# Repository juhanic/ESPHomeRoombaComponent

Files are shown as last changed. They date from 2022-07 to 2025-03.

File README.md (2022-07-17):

# Roomba Component for ESPHome

  This is a quick and dirty update of [davidecavestro's work](https://github.com/davidecavestro/ESPHomeRoombaComponent) with a focus on giving a new user a reasonable chance of getting it working without digging through 100 forum threads. [This thread](https://community.home-assistant.io/t/add-wifi-to-an-older-roomba/23282/158) should be useful should there be any issues. I'll also be including my circuit board design for a small sandwich of boards that fit nicely on top of the roomba.
  
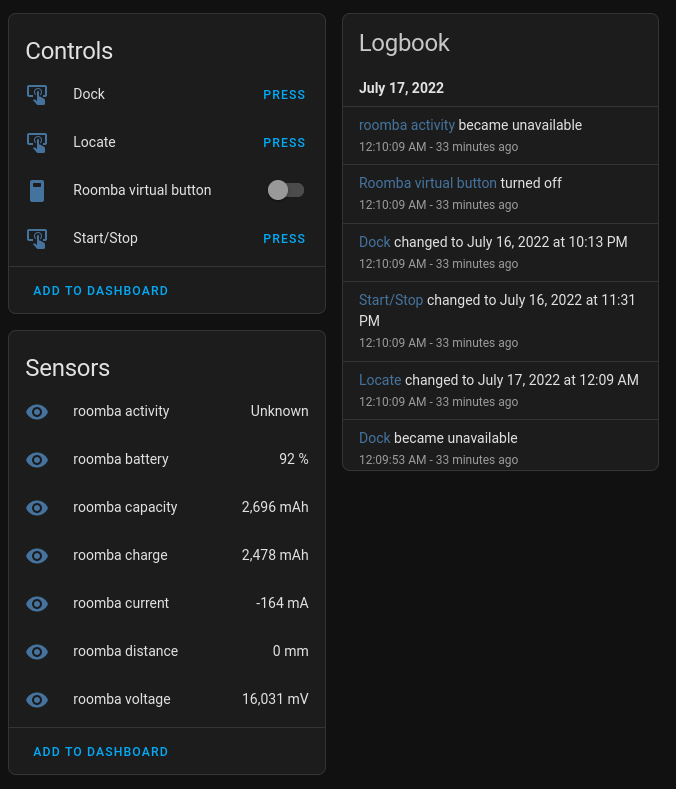
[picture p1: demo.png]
dashboard example
  I've added some notes and updates to the example in the example folder. My example config should get you up and running though there are a few bugs that still need to be worked out. 

  The inspiration is [Mannkind ESPHomeRoombaComponent](https://github.com/mannkind/ESPHomeRoombaComponent), that became deprecated due to dependency updates.
In addition I did not want the Roomba device to communicate over MQTT, it instead registers a service call for commands, and expose sensors through `roomba.yaml`.

## Hardware

## Wiring Guide
Using the brc pin we get the following:
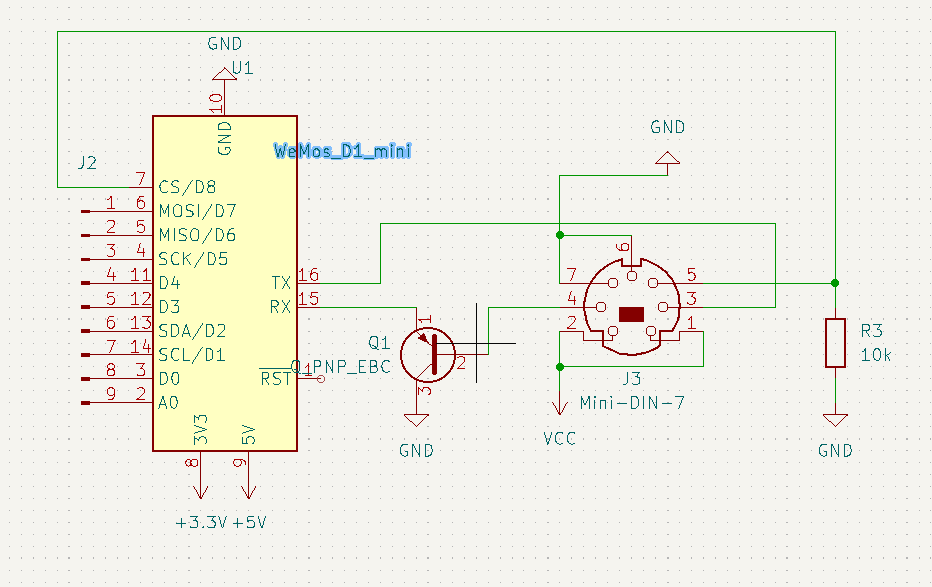
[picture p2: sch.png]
brc wiring

The PNP transistor is necessesary. Resistive dividers are hit or miss and a 2n4403 or a 2n3906 is cheap.

Alternatively using the IR led:
IR wiring

## Special Notes

*Depending on your Roomba model, you might be unlucky as me and have a bug that does not allow the device to wake from brc pin when it goes into passive mode during trickle charging. To circumvent this I copied my code from a previous general controller I had stationed in the kitchen for 433mhz and IR controlling that sends the start code with and IR led to the roomba, it need a clear sight of the roomba IR sensor over a short distance.

If you need this, uncomment the remote transmitter switch section in the `roomba.yaml` and use the switch to wake and clean. 

## Placement

The Wemos D1 mini is small enough to [fit into the compartment by one of the wheels](https://community-home-assistant-assets.s3.dualstack.us-west-2.amazonaws.com/optimized/2X/a/a258c7253f8bd3fe76ad9e7aa1202b60bd113d74_2_496x600.jpg). 
But using a esp-01 or esp-12 series and some single braid wire I have managed to fit it all under the top lid without bulging or deformeties, the only visual defect is my led that is pointing at the IR reciever.

## Custom Circuit Board

This board was designed to be etched at home but could also be ordered from the likes of dirtypcbs.com/ oshpark/ etc.  

If you want to recreate my circuit board exactly, you'll need:  
 - Wemos D1 Mini
 - USB Buck converter
 - 10K Resistor

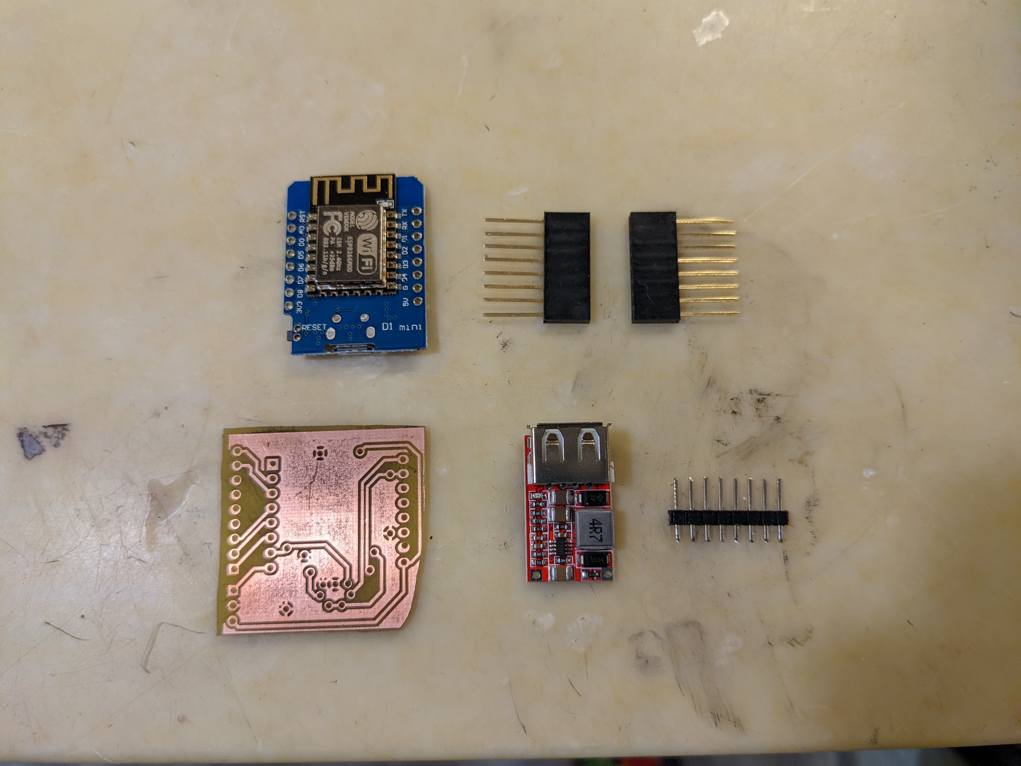
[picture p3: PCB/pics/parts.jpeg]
Parts


Pull 7 Header pins out of the pin headers that came with the Wemos D1 and stick them into the roomba's serial port, then place the board on top and solder the pins in place to get the alignment correct.  

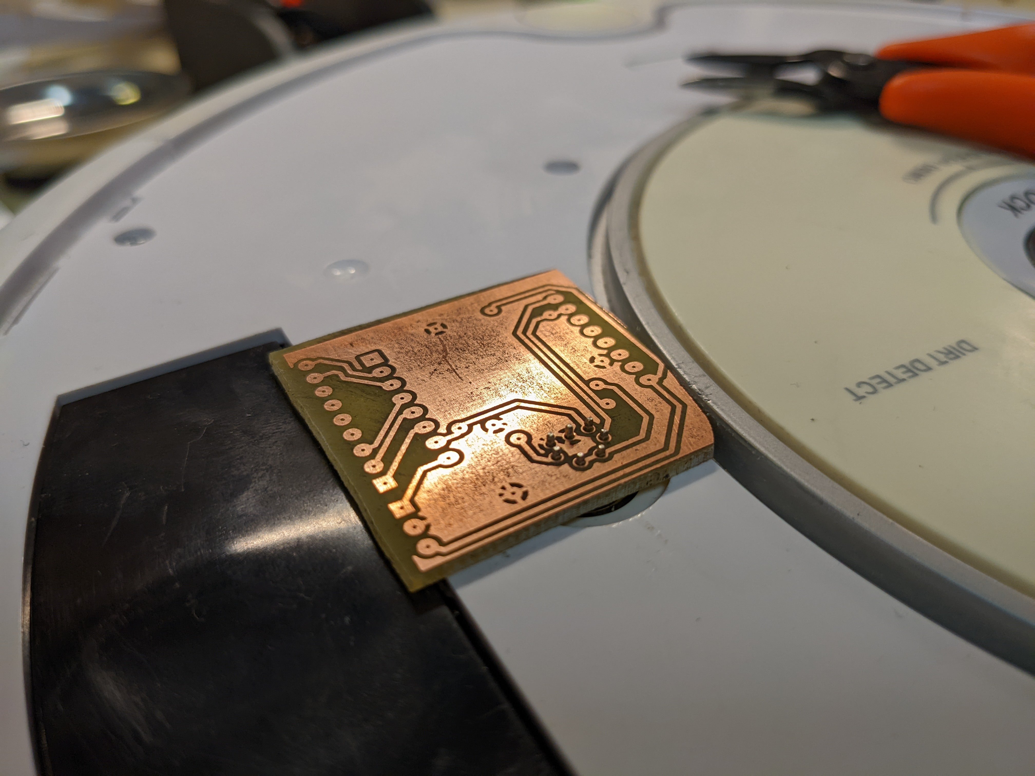
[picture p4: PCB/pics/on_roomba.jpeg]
On Roomba

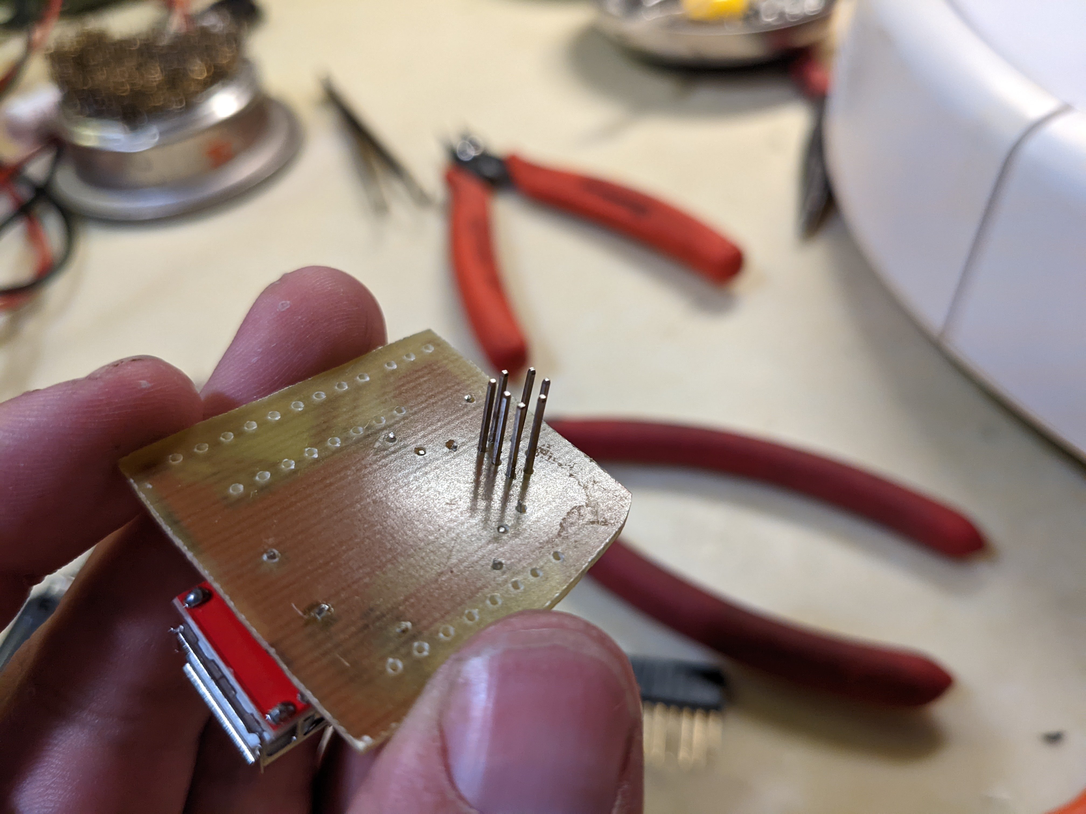
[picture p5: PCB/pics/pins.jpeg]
Pins


The next step is to remove the USB port from the buck converter PCB and stake it in place with 4 header pins, soldering it as close to the roomba PCB as possible.  
After doing that, the resistor and transistor should be fitted into the board.  
The final step is to solder the long headers into the wemos d1 and solder it as close to the roomba PCB as possible. Cut all component leads flush with the bottom of the board to allow the board to seat properly against the roomba. Test for short circuits before plugging it into the roomba!

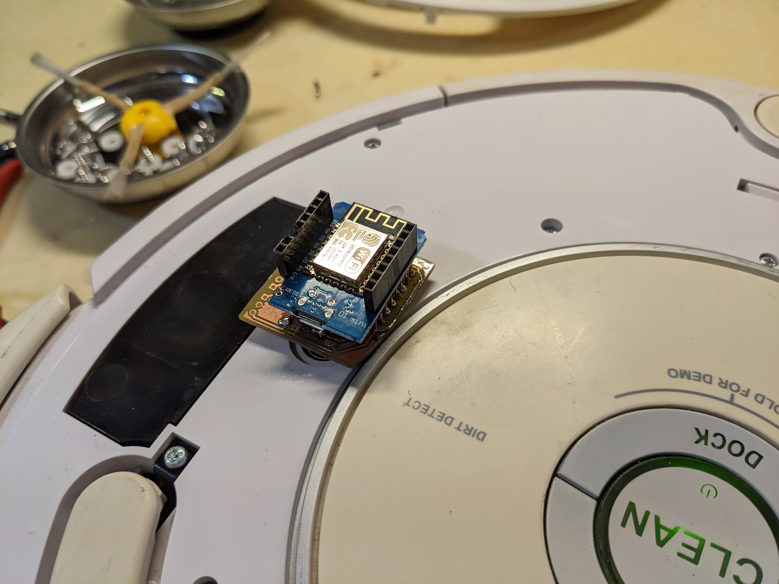
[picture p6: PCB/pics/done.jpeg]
Done


## Software Setup/Use

Copy the contents of the `ESPRoombaHomeComponent.h` and `example/roomba.yaml` into your esphome config folder, change accordingly.

Flash onto new device and connect circuit.

## Motivation

Besides the obvious, connecting your vacuum to your automation system, it also does so completly inside a private and controlled ecosystem. As I was about to replace this unit due to the "hacky feel" of using the IR led, as the unit was shipped bugged and there's not a high availability of create cables for a patch, but all other solutions had me locked into a proprietary system such as mi home, or tuya with smart life; sure there are roundabout ways of both interfacing with them through Home assistant etc, and do so locally. They all seemingly lacked the future proofing and control I wanted. With this setup there is nothing really stopping you from a full on LiDar setup and room control!

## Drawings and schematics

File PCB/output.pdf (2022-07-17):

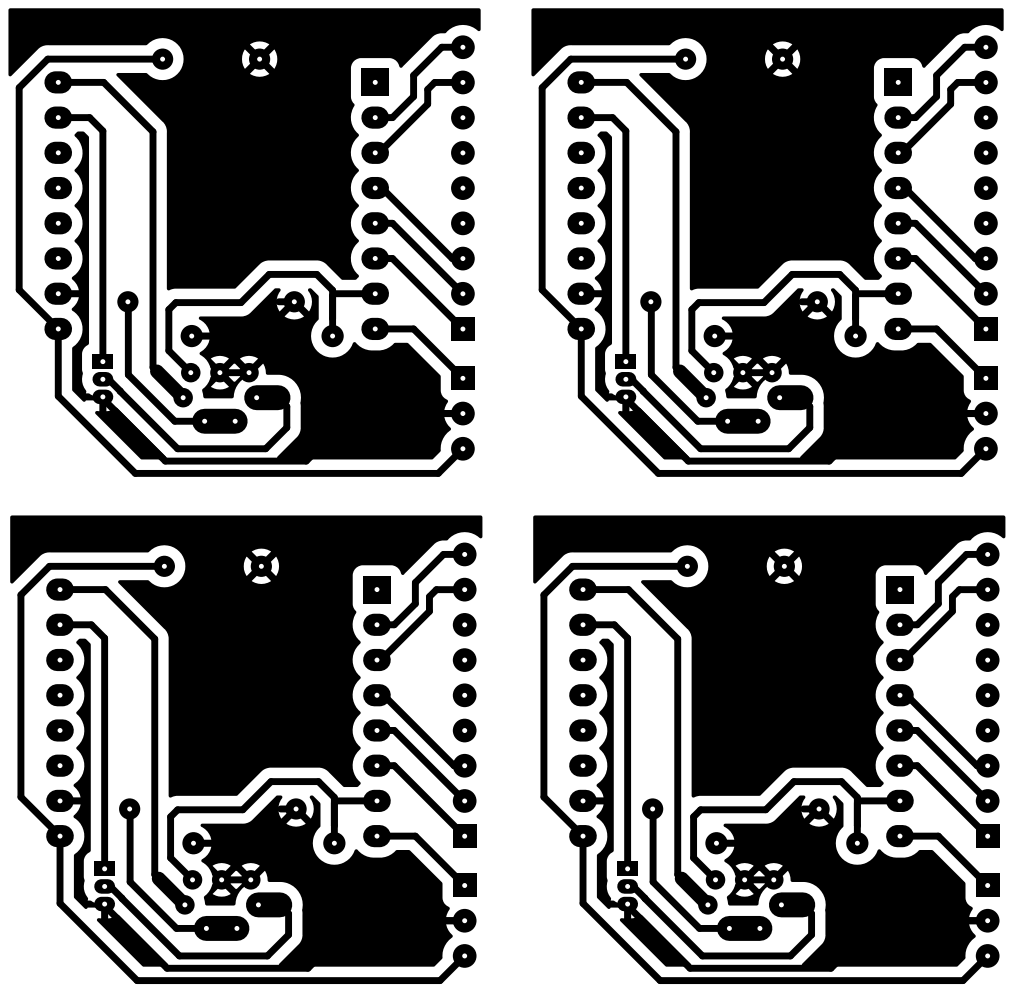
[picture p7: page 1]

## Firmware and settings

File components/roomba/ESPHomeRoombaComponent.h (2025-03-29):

#pragma once

#include "esphome/core/defines.h"
#include "esphome/core/log.h"
#include "esphome/core/hal.h"
#include "esphome/core/component.h"
#include "esphome/components/sensor/sensor.h"
#include "esphome/components/uart/uart.h"
//#include "esphome/components/text_sensor/text_sensor.h"

#define ROOMBA_READ_TIMEOUT 200

namespace esphome {
namespace roomba {

class RoombaComponent : public uart::UARTDevice, public PollingComponent, public sensor::Sensor {
protected:
  InternalGPIOPin * brcPin;
  uint32_t updateInterval;
  sensor::Sensor *distanceSensor;
  sensor::Sensor *voltageSensor;
  sensor::Sensor *currentSensor;
  sensor::Sensor *chargeSensor;
  sensor::Sensor *capacitySensor;
  sensor::Sensor *batteryPercentSensor;
  sensor::Sensor *temperatureSensor;
  //  text_sensor::TextSensor *activitySensor;
 
public:
  void set_distance_sensor(sensor::Sensor *s) { distanceSensor = s; }
  void set_voltage_sensor(sensor::Sensor *s) { voltageSensor = s; }
  void set_current_sensor(sensor::Sensor *s) { currentSensor = s; }
  void set_charge_sensor(sensor::Sensor *s) { chargeSensor = s; }
  void set_capacity_sensor(sensor::Sensor *s) { capacitySensor = s; }
  void set_battery_sensor(sensor::Sensor *s) { batteryPercentSensor = s; }
  void set_temperature_sensor(sensor::Sensor *s) { temperatureSensor = s; }
  //void set_activity_sensor(text_sensor::TextSensor *s) { activitySensor = s; }
  void set_brc_pin(InternalGPIOPin *pin) { brcPin = pin; }
  void brc_wakeup() {
    // Roomba Wakeup
    brcPin->digital_write(false);
    delay(500);
    brcPin->digital_write(true);
    delay(100);
  }

  void flush() {
    while (available()) {
      read();
    }
  }

  void setup() override {
    brcPin->pin_mode(gpio::FLAG_OUTPUT);
    brcPin->digital_write(true);
  }

  void update() override {
    uint8_t charging;
    uint16_t voltage;
    int16_t current;
    uint16_t batteryCharge;
    uint16_t batteryCapacity;
    int16_t distance;
    int8_t temperature;

    flush();

    uint8_t sensors[] = {
      SensorChargingState,
      SensorVoltage,
      SensorCurrent,
      SensorBatteryCharge,
      SensorBatteryCapacity,
      SensorDistance,
      SensorBatteryTemperature
    };
    uint8_t values[] = {0, 0, 0, 0, 0, 0, 0, 0, 0, 0, 0, 0};

    bool success = getSensorsList(sensors, sizeof(sensors), values, sizeof(values));
    if (!success) {
      ESP_LOGD("custom", "Could not get sensor values from serial");
      return;
    }

    charging = values[0];
    voltage = values[1] * 256 + values[2];
    current = values[3] * 256 + values[4];
    batteryCharge = values[5] * 256 + values[6];
    batteryCapacity = values[7] * 256 + values[8];
    distance = values[9] * 256 + values[10];
    temperature = values[11];
    std::string activity = this->get_activity(charging, current);
    // Only publish new states if there was a change
    if (this->distanceSensor && this->distanceSensor->state != distance)
      this->distanceSensor->publish_state(distance);

    if (this->voltageSensor && this->voltageSensor->state != voltage)
      this->voltageSensor->publish_state(voltage);

    if (this->currentSensor && this->currentSensor->state != current)
      this->currentSensor->publish_state(current);

    if (this->chargeSensor && this->chargeSensor->state != batteryCharge)
      this->chargeSensor->publish_state(batteryCharge);

    if (this->capacitySensor && this->capacitySensor->state != batteryCapacity)
      this->capacitySensor->publish_state(batteryCapacity);

    float battery_level = 100.0 * ((1.0 * batteryCharge) / (1.0 * batteryCapacity));
    if (this->batteryPercentSensor && this->batteryPercentSensor->state != battery_level)
      this->batteryPercentSensor->publish_state(battery_level);

    if (this->temperatureSensor && this->temperatureSensor->state != temperature)
      this->temperatureSensor->publish_state(temperature);

    //if (activity.compare(this->activitySensor->state) == 0)
    //      if (this->activitySensor)
    //      this->activitySensor->publish_state(activity);
  }

private:
  typedef enum {
    Sensors7to26					= 0,  //00
    Sensors7to16					= 1,  //01
    Sensors17to20					= 2,  //02
    Sensors21to26					= 3,  //03
    Sensors27to34					= 4,  //04
    Sensors35to42					= 5,  //05
    Sensors7to42					= 6,  //06
    SensorBumpsAndWheelDrops		= 7,  //07
    SensorWall						= 8,  //08
    SensorCliffLeft					= 9,  //09
    SensorCliffFrontLeft			= 10, //0A
    SensorCliffFrontRight			= 11, //0B
    SensorCliffRight				= 12, //0C
    SensorVirtualWall				= 13, //0D
    SensorOvercurrents				= 14, //0E
    //SensorUnused1					= 15, //0F
    //SensorUnused2					= 16, //10
    SensorIRByte					= 17, //11
    SensorButtons					= 18, //12
    SensorDistance					= 19, //13
    SensorAngle						= 20, //14
    SensorChargingState				= 21, //15
    SensorVoltage					= 22, //16
    SensorCurrent					= 23, //17
    SensorBatteryTemperature		= 24, //18
    SensorBatteryCharge				= 25, //19
    SensorBatteryCapacity			= 26, //1A
    SensorWallSignal				= 27, //1B
    SensoCliffLeftSignal			= 28, //1C
    SensoCliffFrontLeftSignal		= 29, //1D
    SensoCliffFrontRightSignal		= 30, //1E
    SensoCliffRightSignal			= 31, //1F
    SensorUserDigitalInputs			= 32, //20
    SensorUserAnalogInput			= 33, //21
    SensorChargingSourcesAvailable	= 34, //22
    SensorOIMode					= 35, //23
    SensorSongNumber				= 36, //24
    SensorSongPlaying				= 37, //25
    SensorNumberOfStreamPackets		= 38, //26
    SensorVelocity					= 39, //27
    SensorRadius					= 40, //28
    SensorRightVelocity				= 41, //29
    SensorLeftVelocity				= 42, //2A
  } SensorCode;

  typedef enum {
    ChargeStateNotCharging				= 0,
    ChargeStateReconditioningCharging	= 1,
    ChargeStateFullCharging				= 2,
    ChargeStateTrickleCharging			= 3,
    ChargeStateWaiting					= 4,
    ChargeStateFault					= 5,
  } ChargeState;
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

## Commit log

2022-01-30 re-order charging/docked
2022-01-30 Add batterytemperature sensor
2022-07-17 Added schematic
2022-07-17 Added PCB
    [panel.kicad_pcb, roomborg.kicad_pcb, roomborg.kicad_sch]
2022-07-17 PCB documentation
2022-07-17 Added some filtering to example config
2022-07-17 Fixed activity sensor
